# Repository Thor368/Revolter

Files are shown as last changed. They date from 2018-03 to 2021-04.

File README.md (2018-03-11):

# Revolter 100V
Fork of the original HSWR Version 2 to support up to 100V and two TO-220 MOSFET packages.

#Work in progress

# TODO

## V1.0
- first prerealse at alpha stage
- some bugs but works

## V1.1
- did an great overhaul of high current paths
- fixed wrong 3V3 reg pin out
- blew the IO connector up to 8 pins (turns out 7pin is rare)
- changed shunt to 2512
- changed hf caps to double 1210
- two input caps
- pin outs for all IO on silk screen
- spread the references so you can actually read them
- connected the Hall/Temp pull-ups to 3V3 instead of 5V

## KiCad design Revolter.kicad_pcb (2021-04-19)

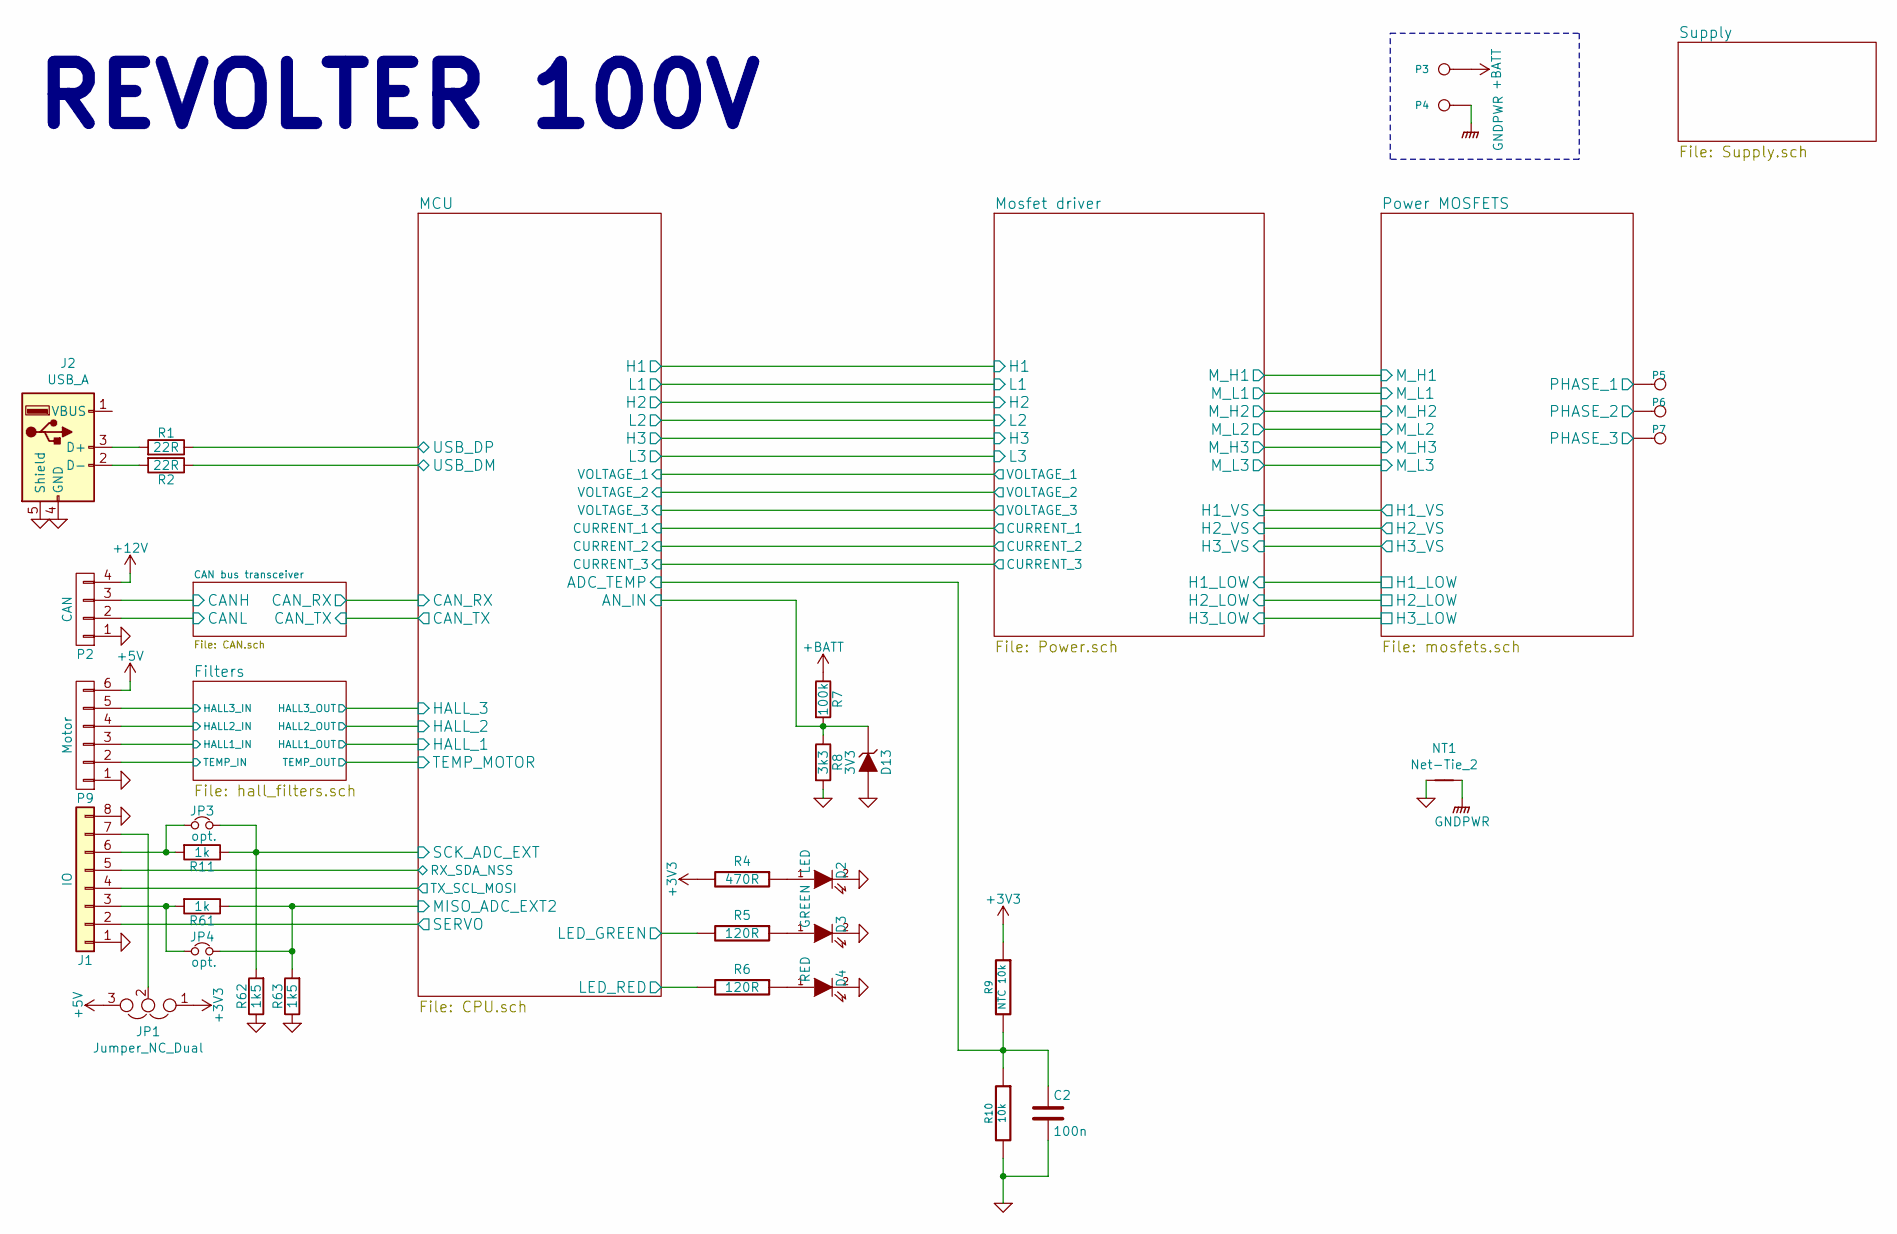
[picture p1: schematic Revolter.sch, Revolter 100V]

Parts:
C2: 100n; C_0805_2012Metric
D2: LED; LED_0805_2012Metric
D3: GREEN; LED_0805_2012Metric
D4: RED; LED_0805_2012Metric
D13: 3V3; D_SOD-123
J1: IO; PhoenixContact_MCV_1,5_8-G-3.5_1x08_P3.50mm_Vertical
J2: USB_A; USB_B_TE_5787834_Vertical
JP1: Jumper_NC_Dual; SolderJumper-3_P1.3mm_Open_RoundedPad1.0x1.5mm
JP3, JP4: opt.; SolderJumper-2_P1.3mm_Open_RoundedPad1.0x1.5mm
NT1: Net-Tie_2; NetTie-2_SMD_Pad0.5mm
P2: CAN; PhoenixContact_MCV_1,5_4-G-3.5_1x04_P3.50mm_Vertical
P3: IN+; MountingHole_3.2mm_M3_Pad_Via
P4: IN-; MountingHole_3.2mm_M3_Pad_Via
P5: MOTOR3; MountingHole_3.2mm_M3_Pad_Via
P6: MOTOR2; MountingHole_3.2mm_M3_Pad_Via
P7: MOTOR1; MountingHole_3.2mm_M3_Pad_Via
P9: Motor; PhoenixContact_MCV_1,5_6-G-3.5_1x06_P3.50mm_Vertical
R1, R2: 22R; R_0805_2012Metric
R4: 470R; R_0805_2012Metric
R5, R6: 120R; R_0805_2012Metric
R7: 100k; R_0805_2012Metric
R8: 3k3; R_0805_2012Metric
R9: NTC 10k; R_0603_1608Metric
R10: 10k; R_0805_2012Metric
R11, R61: 1k; R_0805_2012Metric
R62, R63: 1k5; R_0805_2012Metric

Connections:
+3V3: JP1.1, R4.2, R9.1; also elsewhere on the board
+5V: JP1.3, P9.6; also elsewhere on the board
+12V: P2.4; also elsewhere on the board
+BATT: P3.1, R7.1; also elsewhere on the board
/CAN bus transceiver/CANH: P2.3; also elsewhere on the board
/CAN bus transceiver/CANL: P2.2; also elsewhere on the board
/Filters/HALL1_IN: P9.3; also elsewhere on the board
/Filters/HALL2_IN: P9.4; also elsewhere on the board
/Filters/HALL3_IN: P9.5; also elsewhere on the board
/Filters/TEMP_IN: P9.2; also elsewhere on the board
/MCU/ADC_TEMP: C2.1, R9.2, R10.1; also elsewhere on the board
/MCU/AN_IN: D13.1 (K), R7.2, R8.1; also elsewhere on the board
/MCU/LED_GREEN: R5.2; also elsewhere on the board
/MCU/LED_RED: R6.2; also elsewhere on the board
/MCU/MISO_ADC_EXT2: JP4.2, R61.1, R63.2; also elsewhere on the board
/MCU/RX_SDA_NSS: J1.5; also elsewhere on the board
/MCU/SCK_ADC_EXT: JP3.2, R11.1, R62.2; also elsewhere on the board
/MCU/SERVO: J1.2; also elsewhere on the board
/MCU/TX_SCL_MOSI: J1.4; also elsewhere on the board
/MCU/USB_DM: R2.1; also elsewhere on the board
/MCU/USB_DP: R1.1; also elsewhere on the board
/Mosfet driver/H1_VS: P5.1; also elsewhere on the board
/Mosfet driver/H2_VS: P6.1; also elsewhere on the board
/Mosfet driver/H3_VS: P7.1; also elsewhere on the board
GND: C2.2, D2.2 (K), D3.2 (K), D4.2 (K), D13.2 (A), J1.1, J1.8, J2.4 (GND), J2.5 (Shield), NT1.1, P2.1, P9.1, R8.2, R10.2, R62.1, R63.1; also elsewhere on the board
GNDPWR: NT1.2, P4.1; also elsewhere on the board
unnamed: D2.1 (A), R4.1
unnamed: D3.1 (A), R5.1
unnamed: D4.1 (A), R6.1
unnamed: J1.3, JP4.1, R61.2
unnamed: J1.6, JP3.1, R11.2
unnamed: J1.7, JP1.2
unnamed: J2.2 (D-), R2.2
unnamed: J2.3 (D+), R1.2

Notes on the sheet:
REVOLTER 100V

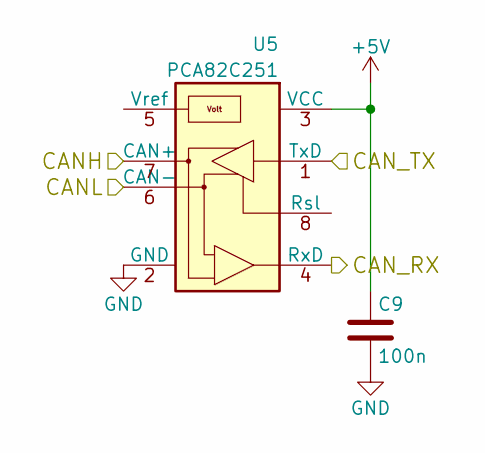
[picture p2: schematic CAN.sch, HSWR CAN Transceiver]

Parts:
C9: 100n; C_0805_2012Metric
U5: PCA82C251; SO-8_3.9x4.9mm_P1.27mm

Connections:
+5V: C9.1, U5.3 (VCC); also elsewhere on the board
/CAN bus transceiver/CANH: U5.7 (CAN+); also elsewhere on the board
/CAN bus transceiver/CANL: U5.6 (CAN-); also elsewhere on the board
/CAN bus transceiver/CAN_RX: U5.4 (RxD); also elsewhere on the board
/CAN bus transceiver/CAN_TX: U5.1 (TxD); also elsewhere on the board
GND: C9.2, U5.2 (GND); also elsewhere on the board

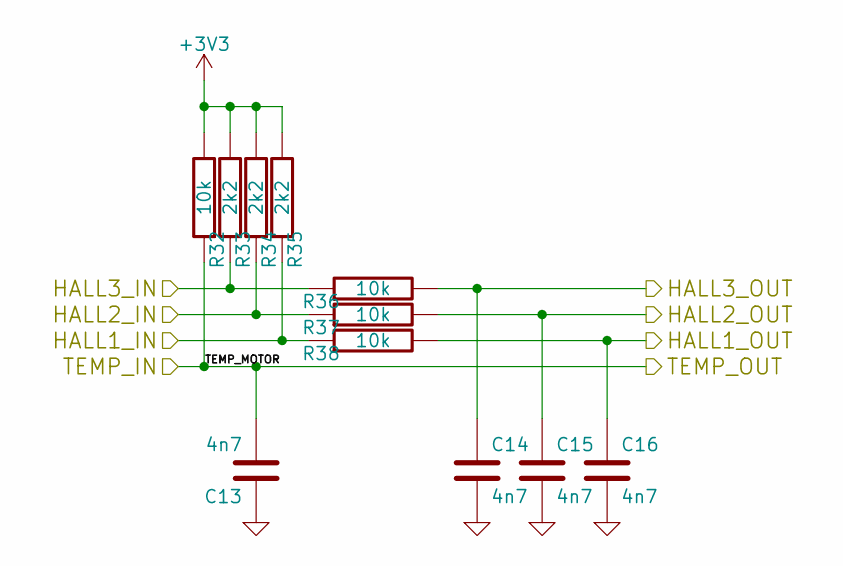
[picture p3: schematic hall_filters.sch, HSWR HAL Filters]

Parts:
C13, C14, C15, C16: 4n7; C_0805_2012Metric
R32, R36, R37, R38: 10k; R_0805_2012Metric
R33, R34, R35: 2k2; R_0805_2012Metric

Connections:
+3V3: R32.2, R33.2, R34.2, R35.2; also elsewhere on the board
/Filters/HALL1_IN: R35.1, R38.1; also elsewhere on the board
/Filters/HALL1_OUT: C16.1, R38.2; also elsewhere on the board
/Filters/HALL2_IN: R34.1, R37.1; also elsewhere on the board
/Filters/HALL2_OUT: C15.1, R37.2; also elsewhere on the board
/Filters/HALL3_IN: R33.1, R36.1; also elsewhere on the board
/Filters/HALL3_OUT: C14.1, R36.2; also elsewhere on the board
/Filters/TEMP_IN: C13.2, R32.1; also elsewhere on the board
GND: C13.1, C14.2, C15.2, C16.2; also elsewhere on the board

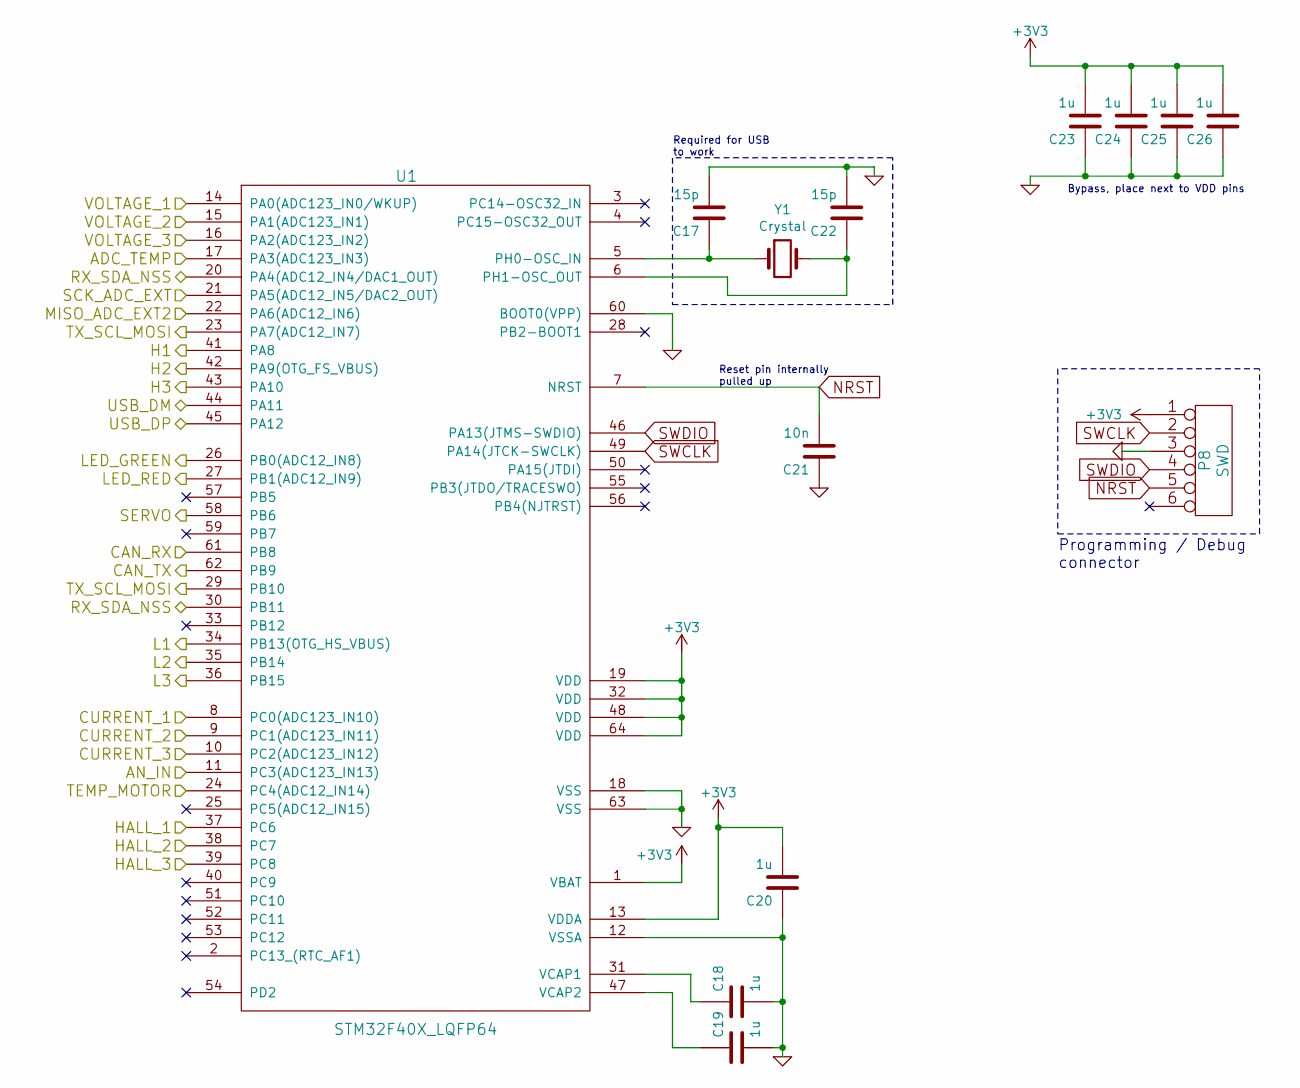
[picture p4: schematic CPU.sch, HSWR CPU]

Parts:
C17, C22: 15p; C_0805_2012Metric
C18, C19, C20, C23, C24, C25, C26: 1u; C_0805_2012Metric
C21: 10n; C_0805_2012Metric
P8: SWD; PinHeader_2x03_P2.54mm_Vertical
U1: STM32F40X_LQFP64; LQFP-64_10x10mm_P0.5mm
Y1: Crystal; Crystal_HC49-U_Vertical

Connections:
+3V3: C20.2, C23.2, C24.2, C25.2, C26.2, P8.1, U1.1 (VBAT), U1.13 (VDDA), U1.19 (VDD), U1.32 (VDD), U1.48 (VDD), U1.64 (VDD); also elsewhere on the board
/CAN bus transceiver/CAN_RX: U1.61 (PB8); also elsewhere on the board
/CAN bus transceiver/CAN_TX: U1.62 (PB9); also elsewhere on the board
/Filters/HALL1_OUT: U1.37 (PC6); also elsewhere on the board
/Filters/HALL2_OUT: U1.38 (PC7); also elsewhere on the board
/Filters/HALL3_OUT: U1.39 (PC8); also elsewhere on the board
/Filters/TEMP_IN: U1.24 (PC4(ADC12_IN14)); also elsewhere on the board
/MCU/ADC_TEMP: U1.17 (PA3(ADC123_IN3)); also elsewhere on the board
/MCU/AN_IN: U1.11 (PC3(ADC123_IN13)); also elsewhere on the board
/MCU/CURRENT_1: U1.8 (PC0(ADC123_IN10)); also elsewhere on the board
/MCU/CURRENT_2: U1.9 (PC1(ADC123_IN11)); also elsewhere on the board
/MCU/CURRENT_3: U1.10 (PC2(ADC123_IN12)); also elsewhere on the board
/MCU/H1: U1.41 (PA8); also elsewhere on the board
/MCU/H2: U1.42 (PA9(OTG_FS_VBUS)); also elsewhere on the board
/MCU/H3: U1.43 (PA10); also elsewhere on the board
/MCU/L1: U1.34 (PB13(OTG_HS_VBUS)); also elsewhere on the board
/MCU/L2: U1.35 (PB14); also elsewhere on the board
/MCU/L3: U1.36 (PB15); also elsewhere on the board
/MCU/LED_GREEN: U1.26 (PB0(ADC12_IN8)); also elsewhere on the board
/MCU/LED_RED: U1.27 (PB1(ADC12_IN9)); also elsewhere on the board
/MCU/MISO_ADC_EXT2: U1.22 (PA6(ADC12_IN6)); also elsewhere on the board
/MCU/RX_SDA_NSS: U1.20 (PA4(ADC12_IN4/DAC1_OUT)), U1.30 (PB11); also elsewhere on the board
/MCU/SCK_ADC_EXT: U1.21 (PA5(ADC12_IN5/DAC2_OUT)); also elsewhere on the board
/MCU/SERVO: U1.58 (PB6); also elsewhere on the board
/MCU/TX_SCL_MOSI: U1.23 (PA7(ADC12_IN7)), U1.29 (PB10); also elsewhere on the board
/MCU/USB_DM: U1.44 (PA11); also elsewhere on the board
/MCU/USB_DP: U1.45 (PA12); also elsewhere on the board
/MCU/VOLTAGE_1: U1.14 (PA0(ADC123_IN0/WKUP)); also elsewhere on the board
/MCU/VOLTAGE_2: U1.15 (PA1(ADC123_IN1)); also elsewhere on the board
/MCU/VOLTAGE_3: U1.16 (PA2(ADC123_IN2)); also elsewhere on the board
GND: C17.2, C18.2, C19.2, C20.1, C21.1, C22.2, C23.1, C24.1, C25.1, C26.1, P8.3, U1.12 (VSSA), U1.18 (VSS), U1.60 (BOOT0(VPP)), U1.63 (VSS); also elsewhere on the board
NRST: C21.2, P8.5, U1.7 (NRST)
unnamed: C17.1, U1.5 (PH0-OSC_IN), Y1.1
unnamed: C18.1, U1.31 (VCAP1)
unnamed: C19.1, U1.47 (VCAP2)
unnamed: C22.1, U1.6 (PH1-OSC_OUT), Y1.2
SWCLK: P8.2, U1.49 (PA14(JTCK-SWCLK))
SWDIO: P8.4, U1.46 (PA13(JTMS-SWDIO))

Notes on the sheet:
Programming / Debug connector
Reset pin internally pulled up
Required for USB to work
Bypass, place next to VDD pins

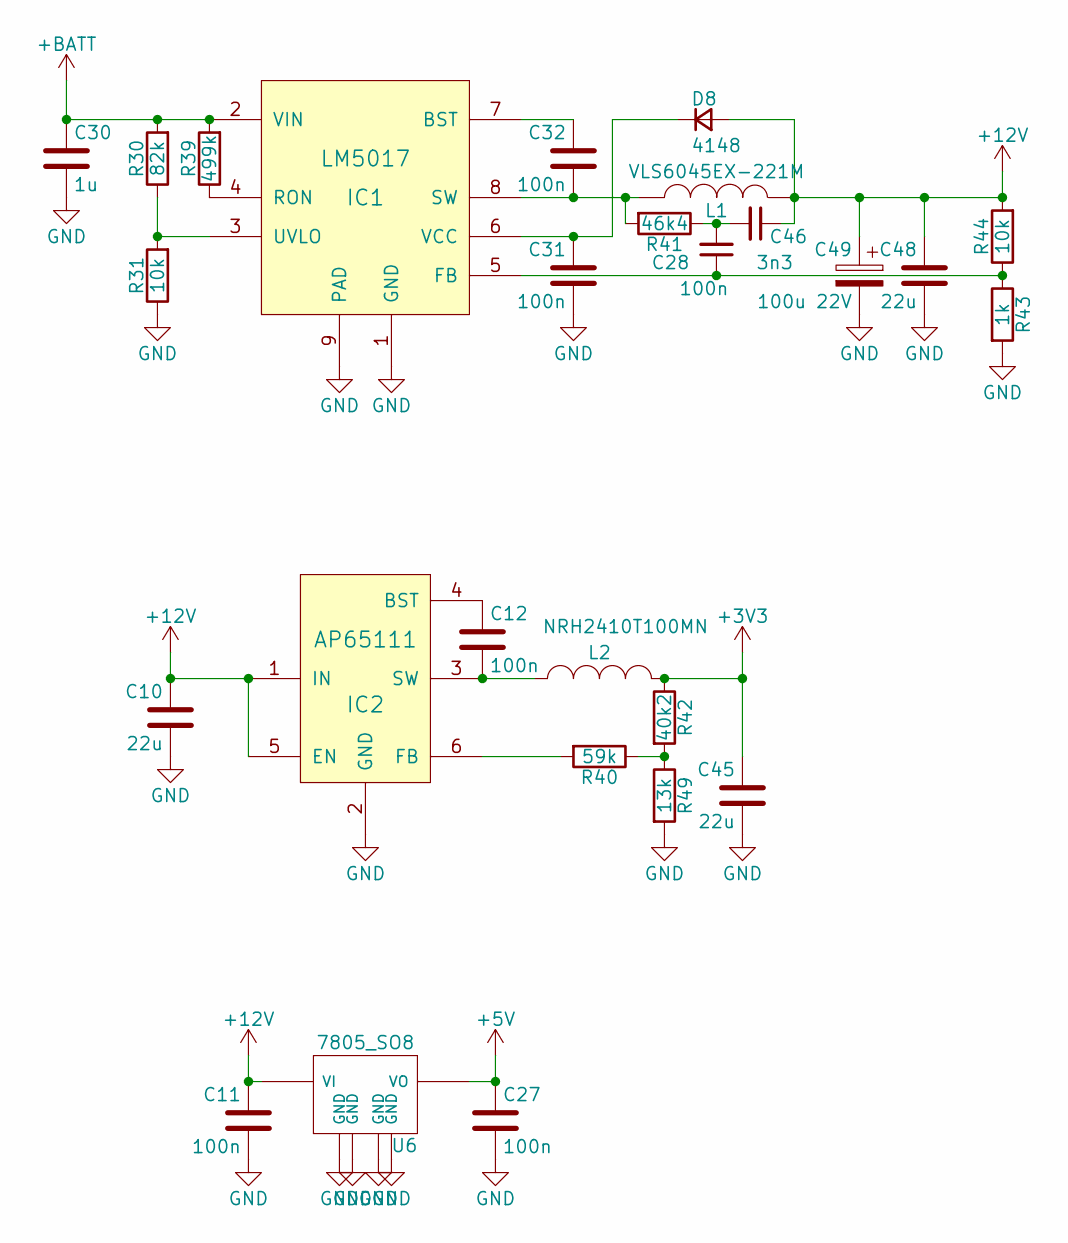
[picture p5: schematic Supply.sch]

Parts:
C10, C45, C48: 22u; C_0805_2012Metric
C11, C12, C27, C28, C31, C32: 100n; C_0805_2012Metric
C30: 1u; C_1206_3216Metric
C46: 3n3; C_0805_2012Metric
C49: 100u 22V; CP_Radial_D6.3mm_P2.50mm
D8: 4148; D_MiniMELF
IC1: LM5017; HSOP-8-1EP_3.9x4.9mm_P1.27mm_EP2.41x3.1mm
IC2: AP65111; SOT-23-6
L1: VLS6045EX-221M; L_Taiyo-Yuden_NR-60xx_HandSoldering
L2: NRH2410T100MN; L_Taiyo-Yuden_NR-24xx_HandSoldering
R30: 82k; R_0805_2012Metric
R31, R44: 10k; R_0805_2012Metric
R39: 499k; R_0805_2012Metric
R40: 59k; R_0805_2012Metric
R41: 46k4; R_0805_2012Metric
R42: 40k2; R_0805_2012Metric
R43: 1k; R_0805_2012Metric
R49: 13k; R_0805_2012Metric
U6: 7805_SO8; SO-8_3.9x4.9mm_P1.27mm

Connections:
+3V3: C45.1, L2.2, R42.1; also elsewhere on the board
+5V: C27.1, U6.8 (VO); also elsewhere on the board
+12V: C10.1, C11.1, C46.1, C48.1, C49.1, D8.2 (A), IC2.1 (IN), IC2.5 (EN), L1.1, R44.2, U6.1 (VI); also elsewhere on the board
+BATT: C30.1, IC1.2 (VIN), R30.2, R39.2; also elsewhere on the board
GND: C10.2, C11.2, C27.2, C30.2, C31.2, C45.2, C48.2, C49.2, IC1.1 (GND), IC1.9 (PAD), IC2.2 (GND), R31.1, R43.2, R49.2, U6.2 (GND), U6.3 (GND), U6.6 (GND), U6.7 (GND); also elsewhere on the board
unnamed: C12.1, IC2.4 (BST)
unnamed: C12.2, IC2.3 (SW), L2.1
unnamed: C28.1, IC1.5 (FB), R43.1, R44.1
unnamed: C28.2, C46.2, R41.1
unnamed: C31.1, D8.1 (K), IC1.6 (VCC)
unnamed: C32.1, IC1.7 (BST)
unnamed: C32.2, IC1.8 (SW), L1.2, R41.2
unnamed: IC1.3 (UVLO), R30.1, R31.2
unnamed: IC1.4 (RON), R39.1
unnamed: IC2.6 (FB), R40.2
unnamed: R40.1, R42.2, R49.1

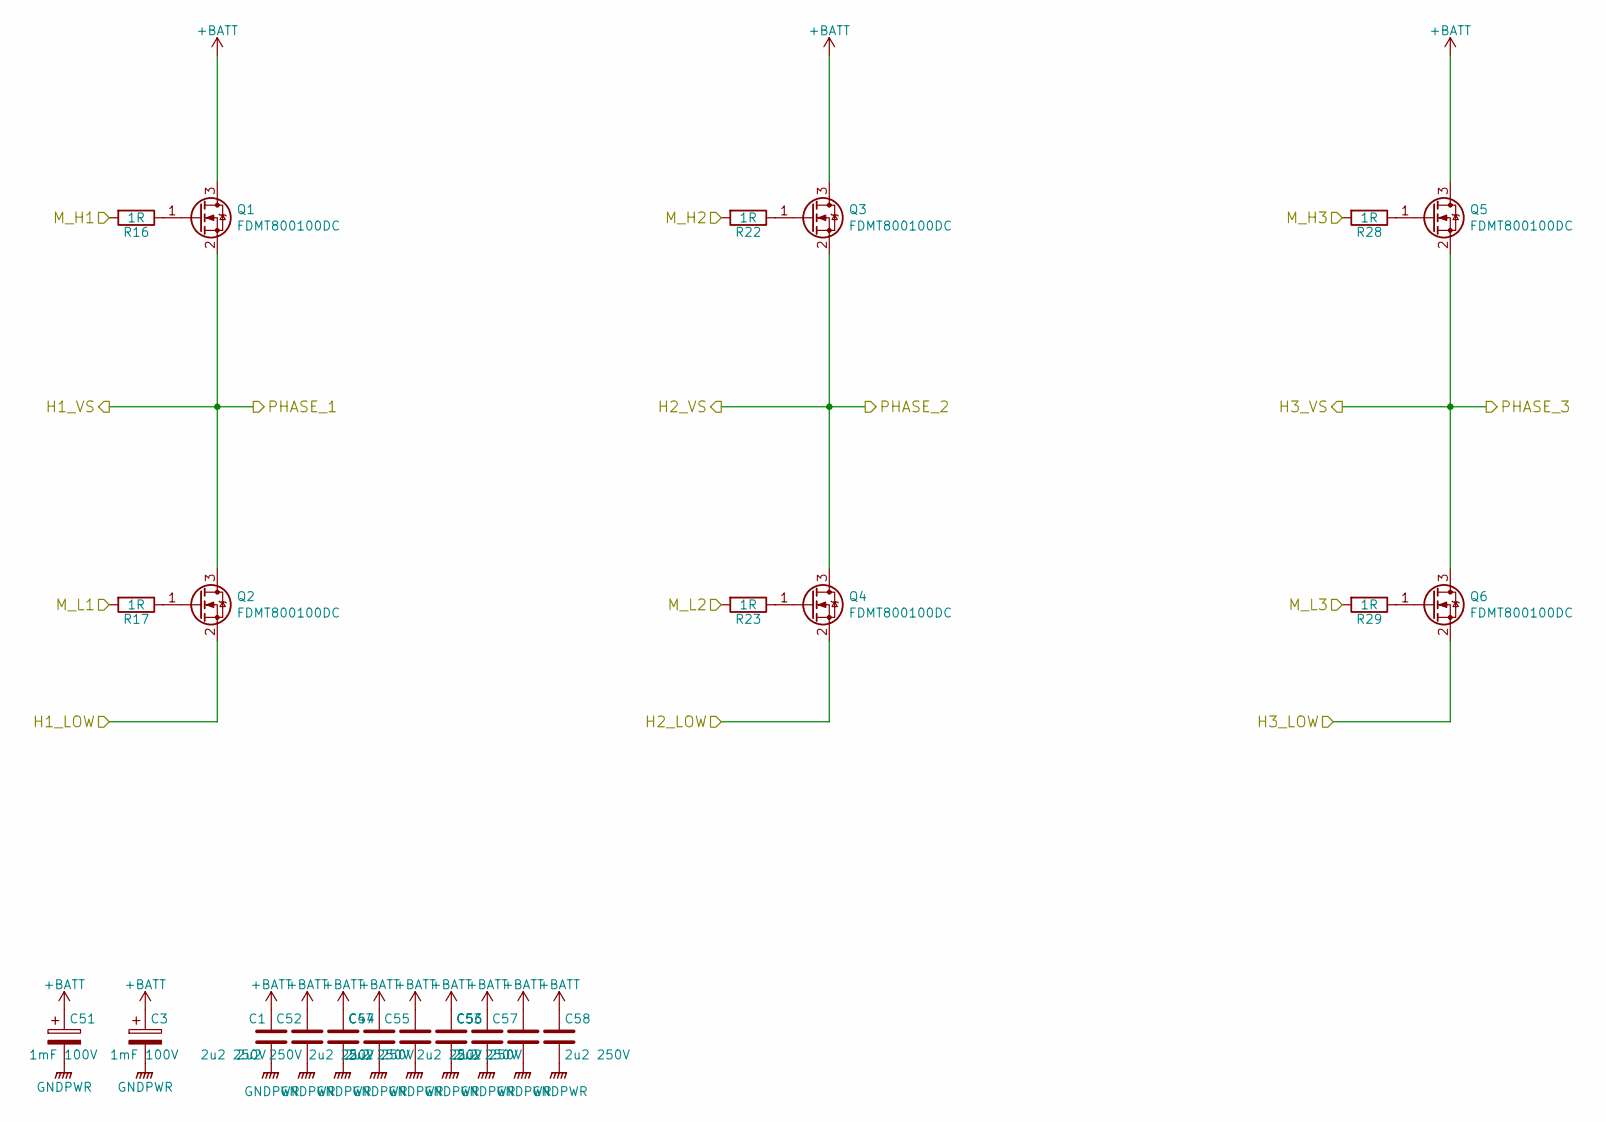
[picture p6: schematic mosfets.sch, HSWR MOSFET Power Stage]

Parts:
C1, C47, C52, C53, C54, C55, C56, C57, C58: 2u2 250V; C_1210_3225Metric
C3, C51: 1mF 100V; CP_Radial_D22.0mm_P10.00mm_SnapIn
Q1, Q2, Q3, Q4, Q5, Q6: FDMT800100DC; PQFN_8x8
R16, R17, R22, R23, R28, R29: 1R; R_0603_1608Metric

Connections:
+BATT: C1.1, C3.1, C47.1, C51.1, C52.1, C53.1, C54.1, C55.1, C56.1, C57.1, C58.1, Q1.3 (D), Q3.3 (D), Q5.3 (D); also elsewhere on the board
/Mosfet driver/H1_LOW: Q2.2 (S); also elsewhere on the board
/Mosfet driver/H1_VS: Q1.2 (S), Q2.3 (D); also elsewhere on the board
/Mosfet driver/H2_LOW: Q4.2 (S); also elsewhere on the board
/Mosfet driver/H2_VS: Q3.2 (S), Q4.3 (D); also elsewhere on the board
/Mosfet driver/H3_LOW: Q6.2 (S); also elsewhere on the board
/Mosfet driver/H3_VS: Q5.2 (S), Q6.3 (D); also elsewhere on the board
/Mosfet driver/M_H1: R16.2; also elsewhere on the board
/Mosfet driver/M_H2: R22.2; also elsewhere on the board
/Mosfet driver/M_H3: R28.2; also elsewhere on the board
/Mosfet driver/M_L1: R17.2; also elsewhere on the board
/Mosfet driver/M_L2: R23.2; also elsewhere on the board
/Mosfet driver/M_L3: R29.2; also elsewhere on the board
GNDPWR: C1.2, C3.2, C47.2, C51.2, C52.2, C53.2, C54.2, C55.2, C56.2, C57.2, C58.2; also elsewhere on the board
unnamed: Q1.1 (G), R16.1
unnamed: Q2.1 (G), R17.1
unnamed: Q3.1 (G), R22.1
unnamed: Q4.1 (G), R23.1
unnamed: Q5.1 (G), R28.1
unnamed: Q6.1 (G), R29.1

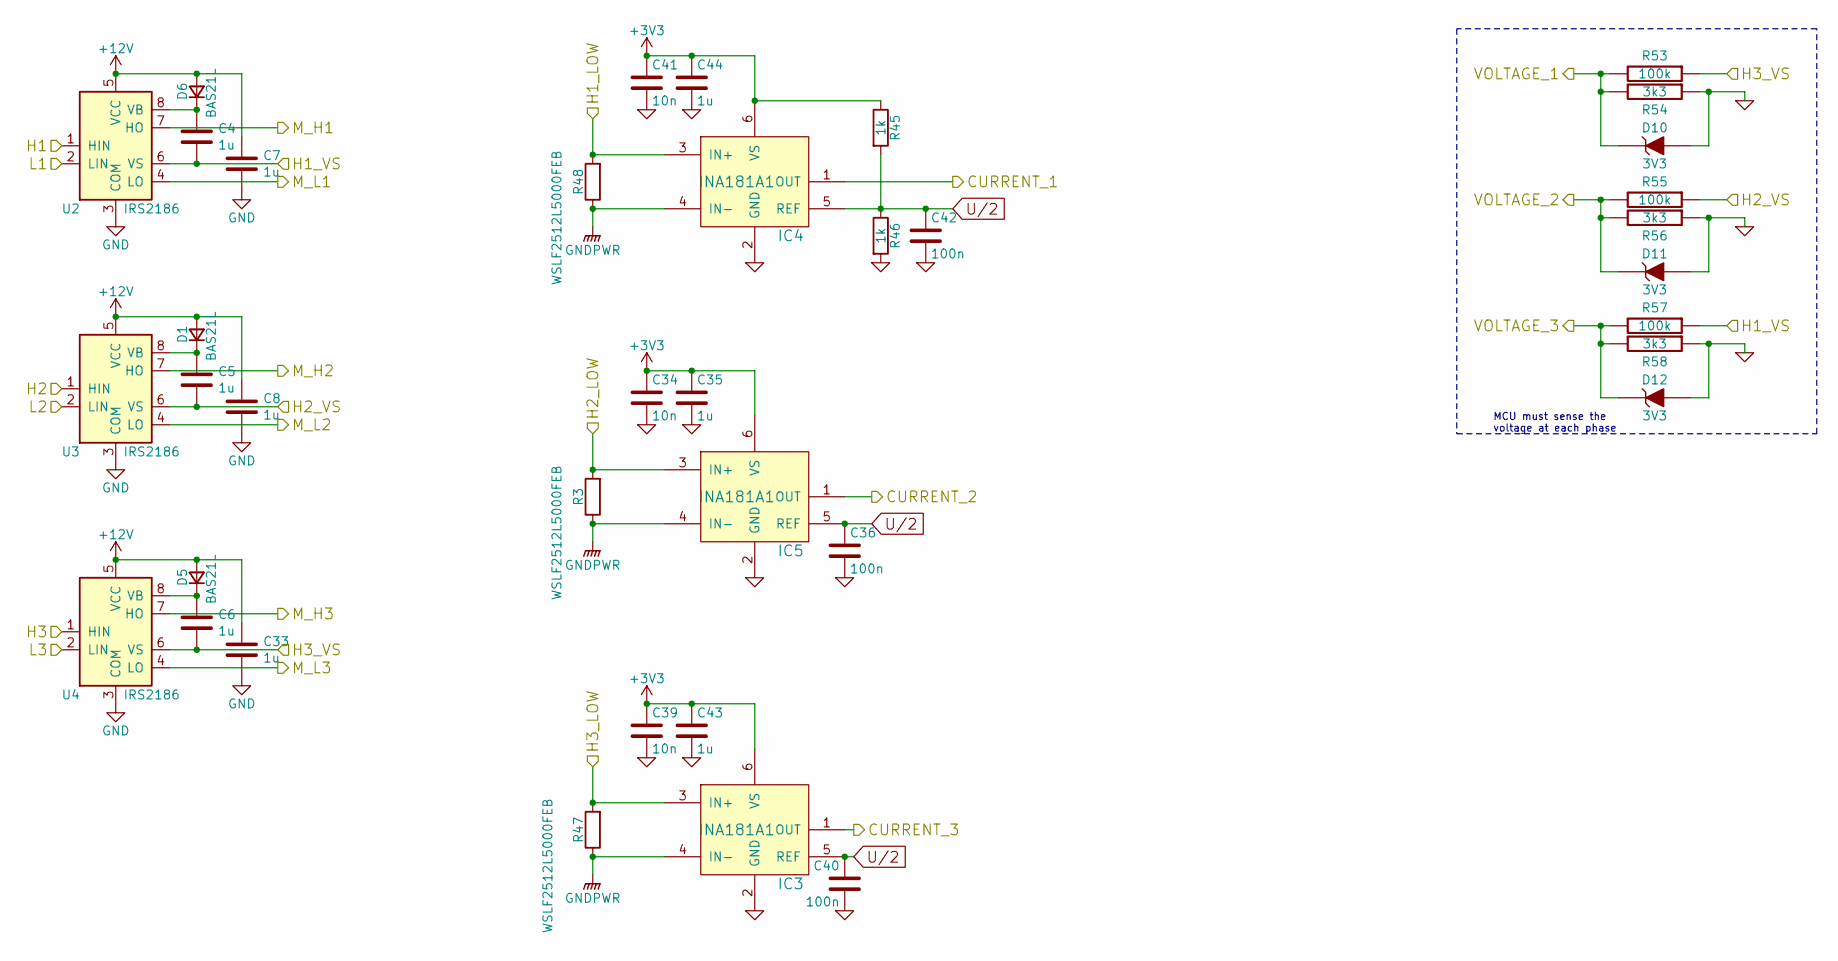
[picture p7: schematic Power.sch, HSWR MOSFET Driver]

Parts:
C4, C5, C6, C7, C8, C33, C35, C43, C44: 1u; C_0805_2012Metric
C34, C39, C41: 10n; C_0805_2012Metric
C36, C40, C42: 100n; C_0805_2012Metric
D1, D5, D6: BAS21L; D_SOT-23_ANK
D10, D11, D12: 3V3; D_SOD-123
IC3, IC4, IC5: INA181A1; SOT-23-6
R3, R47, R48: WSLF2512L5000FEB; R_2512_6332Metric
R45, R46: 1k; R_0805_2012Metric
R53, R55, R57: 100k; R_0805_2012Metric
R54, R56, R58: 3k3; R_0805_2012Metric
U2, U3, U4: IRS2186; SO-8_3.9x4.9mm_P1.27mm

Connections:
+3V3: C34.1, C35.1, C39.1, C41.1, C43.1, C44.1, IC3.6 (VS), IC4.6 (VS), IC5.6 (VS), R45.1; also elsewhere on the board
+12V: C7.1, C8.1, C33.1, D1.2 (A), D5.2 (A), D6.2 (A), U2.5 (VCC), U3.5 (VCC), U4.5 (VCC); also elsewhere on the board
/MCU/CURRENT_1: IC4.1 (OUT); also elsewhere on the board
/MCU/CURRENT_2: IC5.1 (OUT); also elsewhere on the board
/MCU/CURRENT_3: IC3.1 (OUT); also elsewhere on the board
/MCU/H1: U2.1 (HIN); also elsewhere on the board
/MCU/H2: U3.1 (HIN); also elsewhere on the board
/MCU/H3: U4.1 (HIN); also elsewhere on the board
/MCU/L1: U2.2 (LIN); also elsewhere on the board
/MCU/L2: U3.2 (LIN); also elsewhere on the board
/MCU/L3: U4.2 (LIN); also elsewhere on the board
/MCU/VOLTAGE_1: D10.1 (K), R53.2, R54.2; also elsewhere on the board
/MCU/VOLTAGE_2: D11.1 (K), R55.2, R56.2; also elsewhere on the board
/MCU/VOLTAGE_3: D12.1 (K), R57.2, R58.2; also elsewhere on the board
/Mosfet driver/H1_LOW: IC4.3 (IN+), R48.2; also elsewhere on the board
/Mosfet driver/H1_VS: C4.2, R57.1, U2.6 (VS); also elsewhere on the board
/Mosfet driver/H2_LOW: IC5.3 (IN+), R3.2; also elsewhere on the board
/Mosfet driver/H2_VS: C5.2, R55.1, U3.6 (VS); also elsewhere on the board
/Mosfet driver/H3_LOW: IC3.3 (IN+), R47.2; also elsewhere on the board
/Mosfet driver/H3_VS: C6.2, R53.1, U4.6 (VS); also elsewhere on the board
/Mosfet driver/M_H1: U2.7 (HO); also elsewhere on the board
/Mosfet driver/M_H2: U3.7 (HO); also elsewhere on the board
/Mosfet driver/M_H3: U4.7 (HO); also elsewhere on the board
/Mosfet driver/M_L1: U2.4 (LO); also elsewhere on the board
/Mosfet driver/M_L2: U3.4 (LO); also elsewhere on the board
/Mosfet driver/M_L3: U4.4 (LO); also elsewhere on the board
GND: C7.2, C8.2, C33.2, C34.2, C35.2, C36.2, C39.2, C40.2, C41.2, C42.2, C43.2, C44.2, D10.2 (A), D11.2 (A), D12.2 (A), IC3.2 (GND), IC4.2 (GND), IC5.2 (GND), R46.2, R54.1, R56.1, R58.1, U2.3 (COM), U3.3 (COM), U4.3 (COM); also elsewhere on the board
GNDPWR: IC3.4 (IN-), IC4.4 (IN-), IC5.4 (IN-), R3.1, R47.1, R48.1; also elsewhere on the board
unnamed: C4.1, D6.1 (K), U2.8 (VB)
unnamed: C5.1, D1.1 (K), U3.8 (VB)
unnamed: C6.1, D5.1 (K), U4.8 (VB)
U/2: C36.1, C40.1, C42.1, IC3.5 (REF), IC4.5 (REF), IC5.5 (REF), R45.2, R46.1

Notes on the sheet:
MCU must sense the voltage at each phase

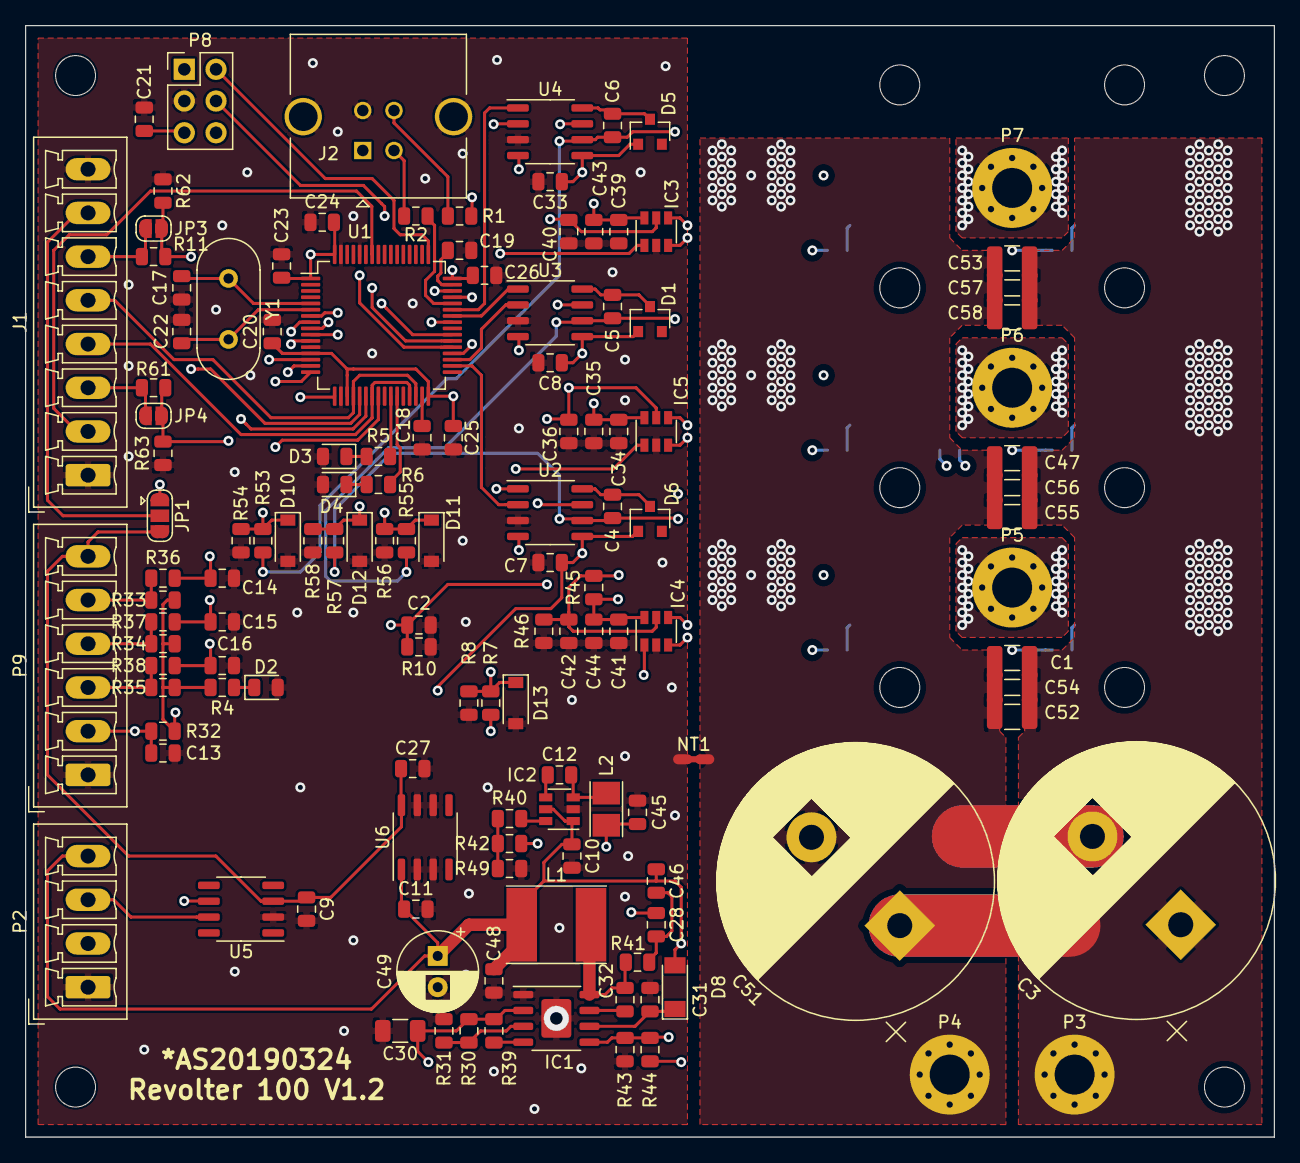
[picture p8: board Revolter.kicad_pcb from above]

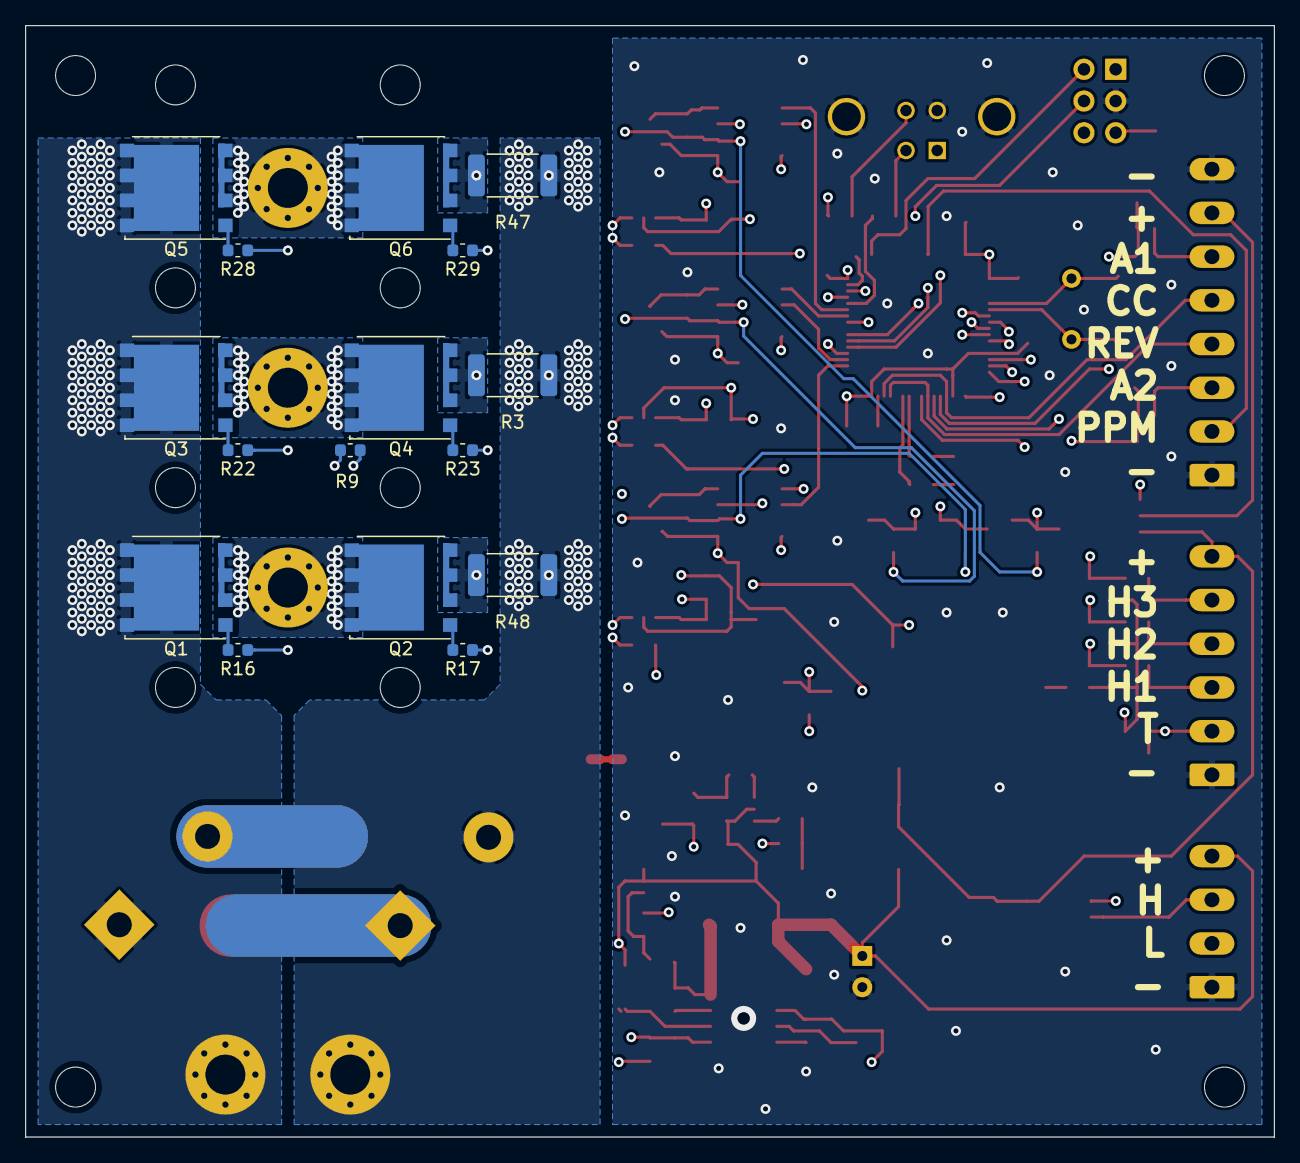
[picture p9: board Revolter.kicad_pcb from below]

Board: 4 copper layers, 100.0 x 89.0 mm, 145 parts (16 on the bottom side), 88 nets.

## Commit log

2017-08-02 - first commit - fork of HSWR V2
    [CAN.sch, CPU.sch, Power.sch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]
2017-09-17 - removed 1 MOSFET of each group (no space) - removed 2 DC buffer caps (no space) - power stage routed - shunts and amps routed - post driver routed - pre driver HV routed
    [CAN.sch, CPU.sch, Power.sch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]
2017-09-21 - redesigned the MOSFET mounting -> minor changes to the power stage - logic and interface routed -> layout finished - needs final check and gerber export
    [CPU.sch, Revolter.kicad_pcb, Revolter.sch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]
2017-09-22 - final check - minor layout cleanups - labeling - first production run => V1.0
    [CPU.sch, Revolter.kicad_pcb, Revolter.sch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]
2018-02-18 - fixed swapped pins 2 and 3 on IC2 - added optional dividers to ADC inputs - made Vcc selectable between 3V3 or 5V
    [CAN.sch, CPU.sch, Power.sch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]
2018-03-11 - basis commit for V1.1 - did an great overhaul of high current paths - fixed wrong 3V3 reg pin out - blew the IO connector up to 8 pins (turns out 7pin is rare) - changed shunt to 2512 - changed hf 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
    [CAN.sch, CPU.sch, Power.sch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]
2018-04-12 - fixed a issue with the central motor phase copper lane - changed text to V1.2
    [Revolter.kicad_pcb]
2018-08-05 - changed dividers to 100k vs 3k3
    [Power.sch, Revolter.kicad_pcb]
2018-08-06 - updated project to 5.0.0 - added some more ignores
    [CAN.sch, CPU.sch, Power.sch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]
2018-08-16 - fixed V_IN ADC channel missing a trace
    [Revolter.kicad_pcb]
2019-03-14 - swapped TO220 dual MOSFET for single DualCool88 MOSFET package - removed postdriver - changed IRS2110 for IRS2186 - added third shunt - rewired CPU for VESC6 compatibility - layout completely from 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
    [CAN.sch, CPU.sch, Power.sch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]
2019-03-20 - added some planes - cleaned some traces - added labels for the connectors
    [Revolter.kicad_pcb]
2019-03-22 - added a via for some plane fills - removed silkscreen labels that don't make sense - widened plane spokes width to 1mm - minor tweaks - added version text - changed plotter settings to use home poi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
    [Revolter.kicad_pcb]
2019-03-24 - fixed some issues with planes - moved some silkscreen labels - updated version/date label
    [Revolter.kicad_pcb]
2019-03-26 - changed ref divider to 1k
    [CAN.sch, Power.sch, Revolter.sch]
2020-06-12 - fixed images display in schematic - added *.sch-bak and fp-info-cache to ignore
    [CAN.sch, CPU.sch, Power.sch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]
2021-04-19 - added some measures in user drawing layer
    [Revolter.kicad_pcb]
